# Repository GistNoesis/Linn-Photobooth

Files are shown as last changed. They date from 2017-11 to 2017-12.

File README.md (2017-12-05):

# Linn Photobooth

LINN is your personal photobooth robot artist. 

A photobooth is a setup where guests take pictures of themselves.

LINN is a 2-axis gimbal controlled by a bluetooth ps3-controller which then stylize your photos with some deep neural style transfer and offer single button instant print experience.

This project was realized in two weeks for the wedding of Thi-Kim & Pierre where it was a great success (lot of fun and interest generated, ~300 pictures taken, ~6000 art pieces created, ~100 prints but we ran out of paper).

Without them this project would never have existed. You can contribute to their wedding gift here : <a href="https://www.paypal.com/cgi-bin/webscr?cmd=_s-xclick&hosted_button_id=3XTEK2FP9ZW2Q"> Donate via Paypal </a>

You can donate to <a href="https://gistnoesis.net/">Gist Noesis</a> on our <a href="https://gistnoesis.net/"> main site </a> or for the photobooth project <a href="https://www.paypal.com/cgi-bin/webscr?cmd=_s-xclick&hosted_button_id=UNQ332GV5MSDU"> here </a>. You can also use the following affiliate links and buy our recommended products to help us improve the photobooth and develop our company. 

You can also help us grow by Starring our repository, sharing it on social media, or even better by building your own Linn.

It's free for non-commercial use. 

It exists in different variants depending on the budget you want to spend, your technical abilities, and the internet connectivity of the event location.

Here is the full setup which went live :

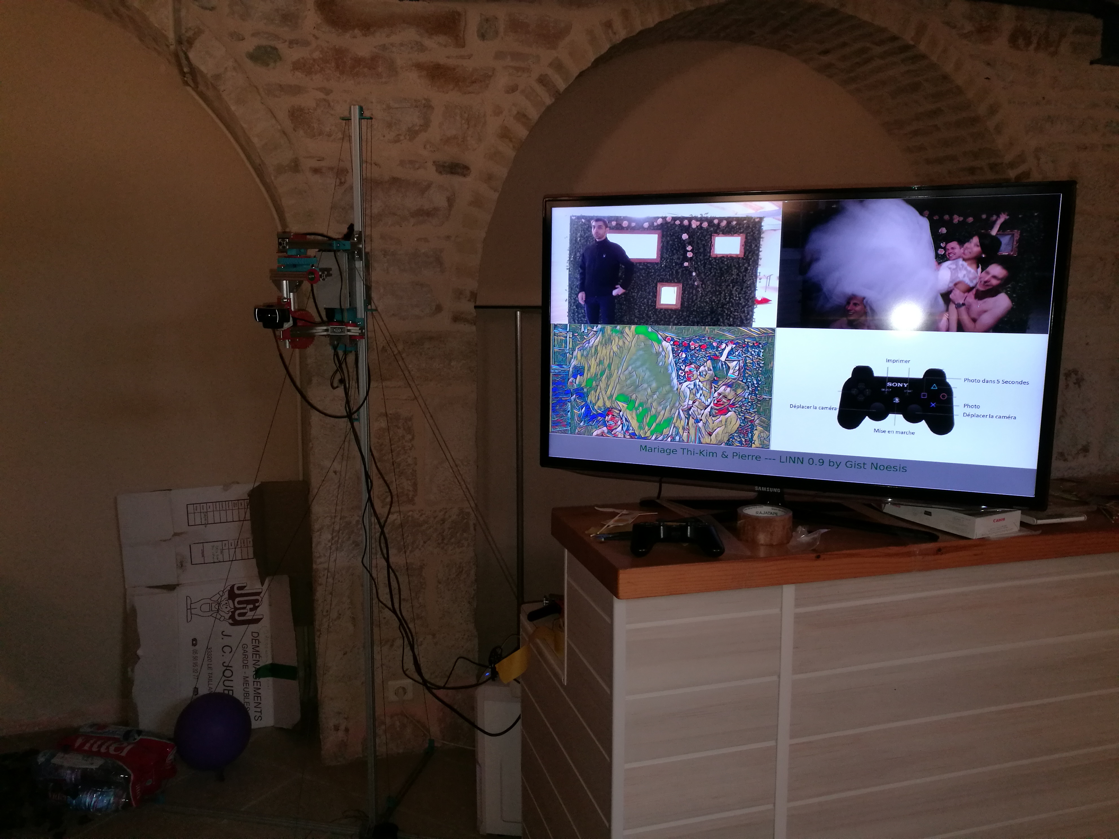
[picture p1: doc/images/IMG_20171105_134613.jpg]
Picture of the full setup


The user experience is intended streamlined : the users put themselves with accessories in the frame of the camera, they see themselves on the TV so they can see what the photo looks like,
 then press X on the controller and it takes a photo instantly displayed. Then they either press Select two times to print the original pictures and 30 secs later they have the printed photo.
Alternatively they can use L2/R2 to change the art style, wait less than 6 secs then press Start two times to print the art picture. 
They can also press "Square" to have the photo taken in 5 secs (enough to hide the ps3 controller).
They can also use L1/R1 to see previous/next pictures.
They can also use the analogic joystick to move the camera.
If you enable manual auto exposure using v4l2-ctl -d /dev/video0 -c exposure_auto=1 then the up and down arrows will adjust exposure time. (Remember you can also adjust Gain using v4l2-ctl to play on ISO sensitivity)

Prototype Demo :

Demo in video (https://www.youtube.com/watch?v=Dvh4kFYVPd0)

Update with GT2 pulley :

Update with GT2 pulley (https://www.youtube.com/watch?v=oYx7XjZQiro)

Advanced human tracking :

Advanced human tracking (https://www.youtube.com/watch?v=4UNtOUySp14)

# Hardware : 
- <a target="_blank" href="https://www.amazon.fr/Manette-PS3-Dual-Shock-noire/dp/B00167U0HY/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">PS3 controller Dual shock 3</a> (I used a controller from my ps3, cheaper clones will probably work, I charged mine and it had enough battery for the night, but you can buy a spare one)
- Bluetooth dongle (<a target="_blank" href="https://www.amazon.fr/Works-BT150-R%C3%A9seau-Adaptateurs-Bluetooth/dp/B00FG2WFE6/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">IT WORKS BT150</a> is lubuntu16.04 compatible It's overpriced but I bought this model at the FNAC to be sure to get it in time, there are probably some compatible bluetooth dongle for a lot cheaper https://doc.ubuntu-fr.org/bluetooth_materiel-soutenu )
- <a target="_blank" href="https://www.amazon.fr/Logitech-C922-Pro-Stream-Webcam/dp/B01L6L52K4/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">Logitech C922</a>
- Canon Selphy CP800
- TV Hd-ready (everything was developped for full HD so I had to adapt the ratio quickly when I discovered my grandparents tv was only Hd-ready )
- <a target="_blank" href="https://www.amazon.fr/Sedatech-PC-GTX1080Ti-CardReader-R%C3%A9solution/dp/B06XJ6431Q/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">Sedatech PC Gamer Ultimate Intel i7-7700K 4x 4.20Ghz (max 4.5Ghz), Geforce GTX1080Ti 11Go, 32Gb RAM DDR4 3000Mhz, 3To HDD, 500Go SSD</a>
- Second <a target="_blank" href="https://www.amazon.fr/MSI-GTX-1080-AERO-11G/dp/B06XT3983Y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">GTX 1080 Ti</a> 11Go Perfect for deep learning. Availability and price varies a lot. 
- 2 axis DIY Gimbal (2 nema 17 stepper (with their cable of appropriate length), <a target="_blank" href="https://www.amazon.fr/gp/product/B018CAVF4E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">RAMPS</a>, <a target="_blank" href="https://www.amazon.fr/Sumvision-Power-Supply-2xSATA-24PIN/dp/B00642F8AU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">PC Power supply</a> (You will need to hack it (by connecting green wire to black (gnd) wire so the power supply start));
<a target="_blank" href="https://www.amazon.fr/LogiLink-CP095-Câble-dalimentation-Schuko-C13/dp/B003Y5IG2W?&_encoding=UTF8&tag=gistnoesis04-21&linkCode=ur2&linkId=aca8e4693b3958e1ad744385ac6ee15e&camp=1642&creative=6746">Power supply cable</a> ; <a target="_blank" href="https://www.amazon.fr/StarTech-com-ATXP4EXT-dextension-dalimentation-processeur/dp/B000O7WFHA/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">ATX extension cable</a>(This cable got damaged during transport and one contact was loose) You can choose longer cables if you don't want to put the power supply near the RAMP board) , 2020 aluminum profiles aluminium brackets screws and nuts (sourced from http://www.systeal.com/fr/ ), ABS 3d printed parts, <a target="_blank" href="https://www.amazon.fr/gp/product/B00EPNN62M/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">608 bearings</a>  , <a target="_blank" href="https://www.amazon.fr/Spectra-Extreme-tresse-tressé-100-m-2000/dp/B01AYUUGYU?&_encoding=UTF8&tag=gistnoesis04-21&linkCode=ur2&linkId=a2e66e39fd9b59a4e716e9a769da290e&camp=1642&creative=6746">150kg dyneema rope</a>) 
- Two 1.8m USB A to B male cables (one for the RAMPS and one for the printer), long enough HDMI cable

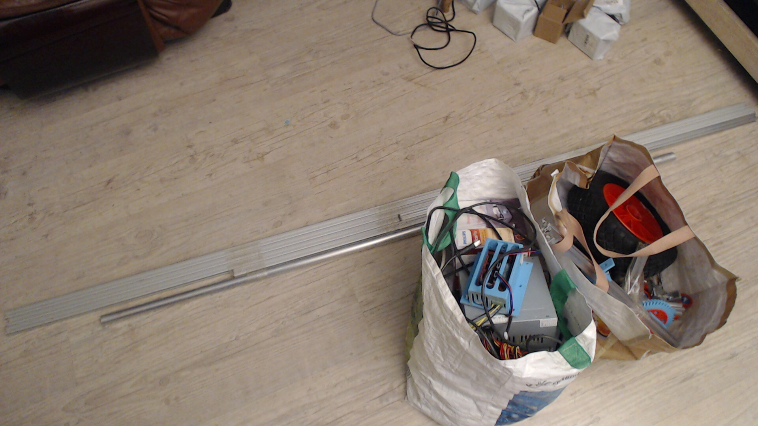
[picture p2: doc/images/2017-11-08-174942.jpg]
Packaged : Electronic in one bag, Mechanical parts and tools in the other bag
 
 Packaged : Electronic in one bag, Mechanical parts and tools in the other bag
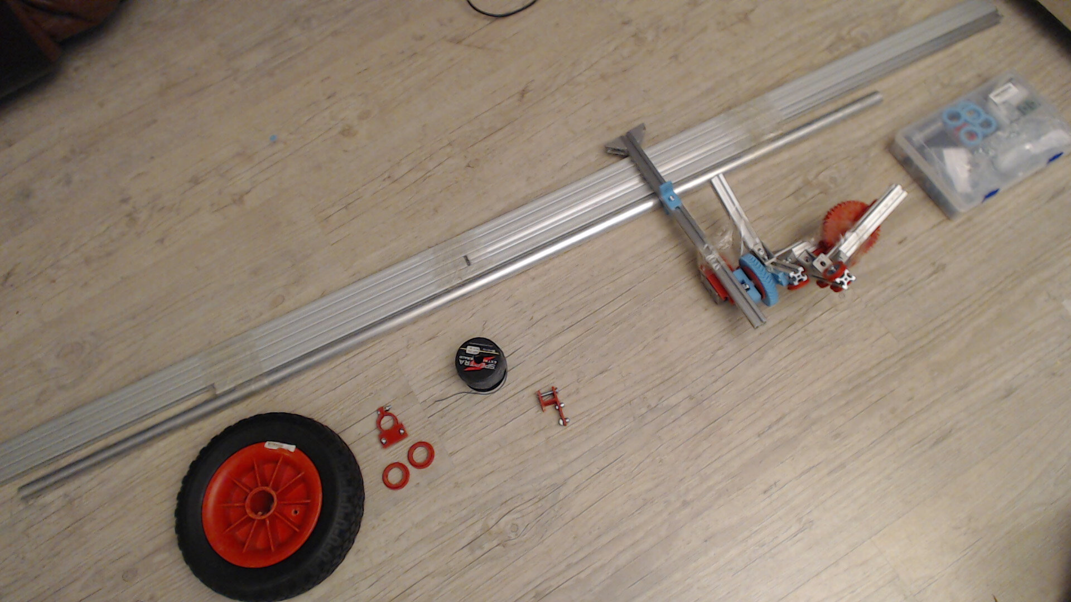
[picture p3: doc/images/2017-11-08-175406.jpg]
Unpacked : Mechanical parts two versions with and without diy gimbal
	
Unpacked : Mechanical parts two versions with and without diy gimbal
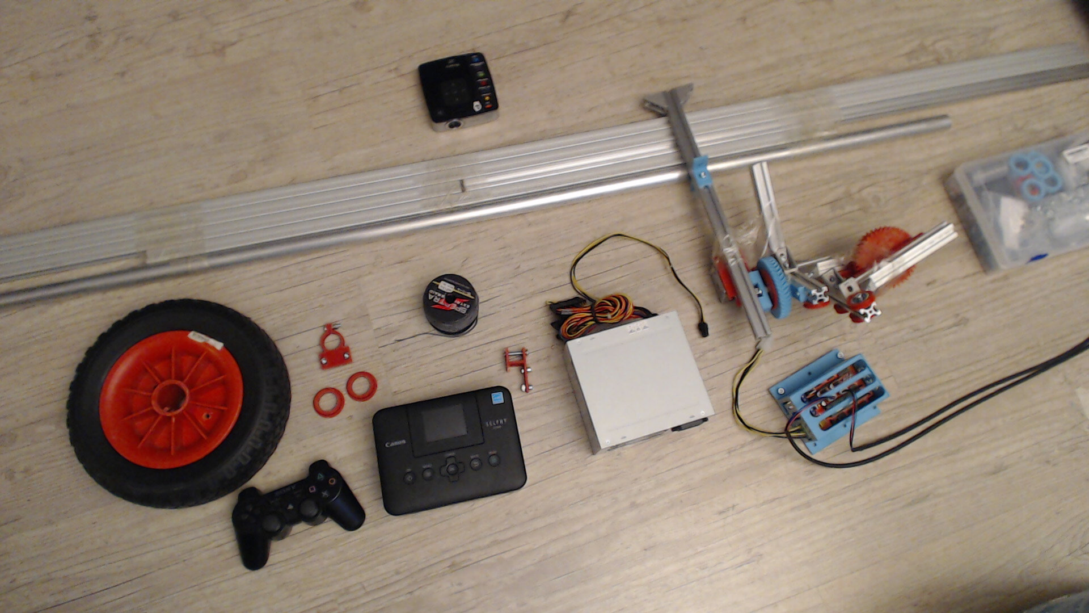
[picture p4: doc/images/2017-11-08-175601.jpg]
Unpacked : Everything except TV, cables and computer
	
Unpacked : Everything except TV, cables and computer
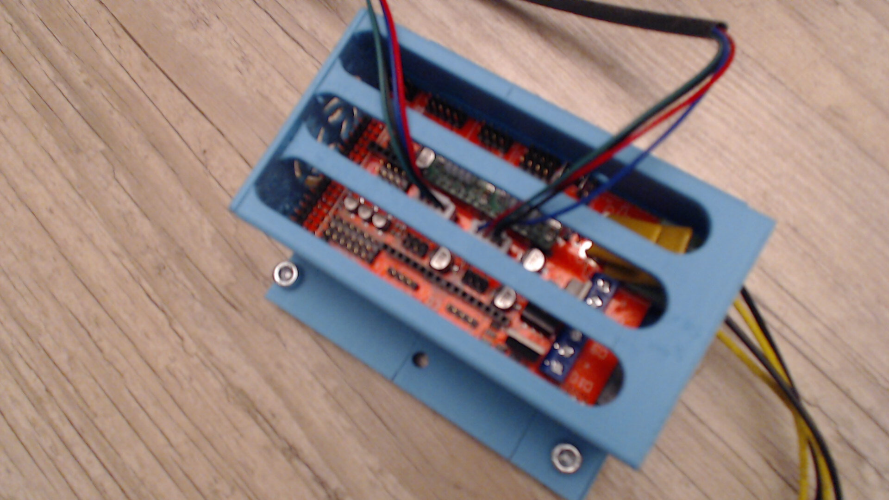
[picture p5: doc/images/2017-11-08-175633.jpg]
close up of the RAMPS board
	
close up of the RAMPS board
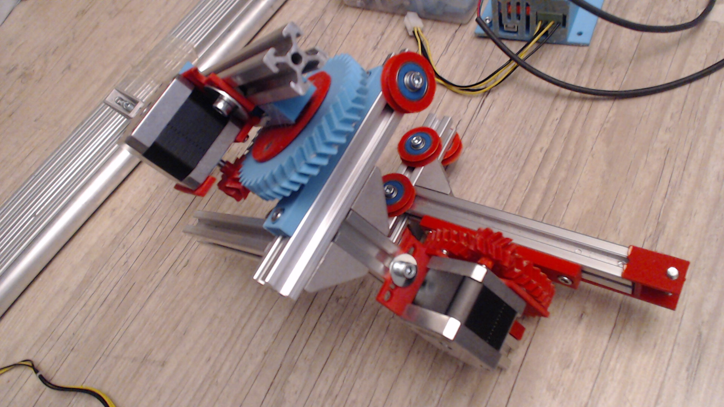
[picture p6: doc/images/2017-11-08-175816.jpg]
close up of diy gimbal
	
close up of diy gimbal
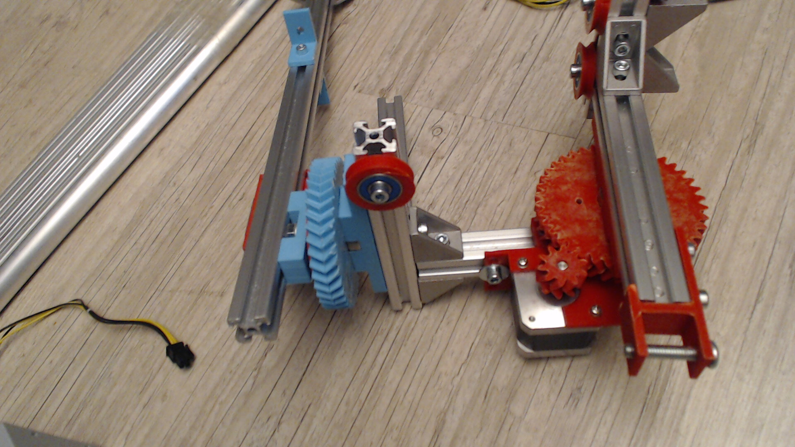
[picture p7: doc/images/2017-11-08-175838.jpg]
close up of diy gimbal other angle
	
close up of diy gimbal other angle
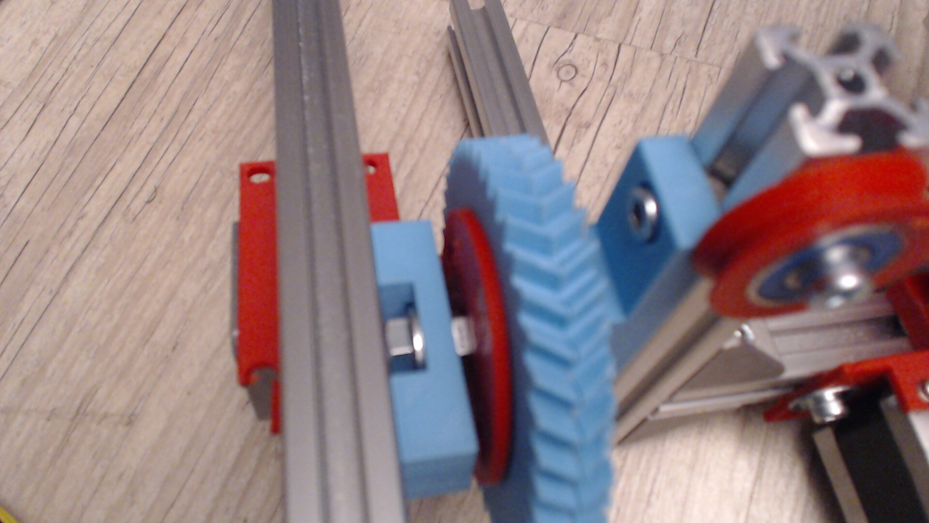
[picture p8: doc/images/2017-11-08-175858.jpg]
close up of one axis of the diy gimbal
	
close up of one axis of the diy gimbal
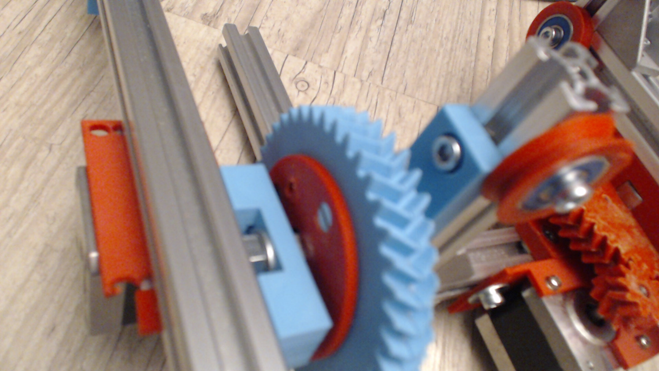
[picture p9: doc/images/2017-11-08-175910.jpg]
close up of one axis of the diy gimbal other angle
	
close up of one axis of the diy gimbal other angle
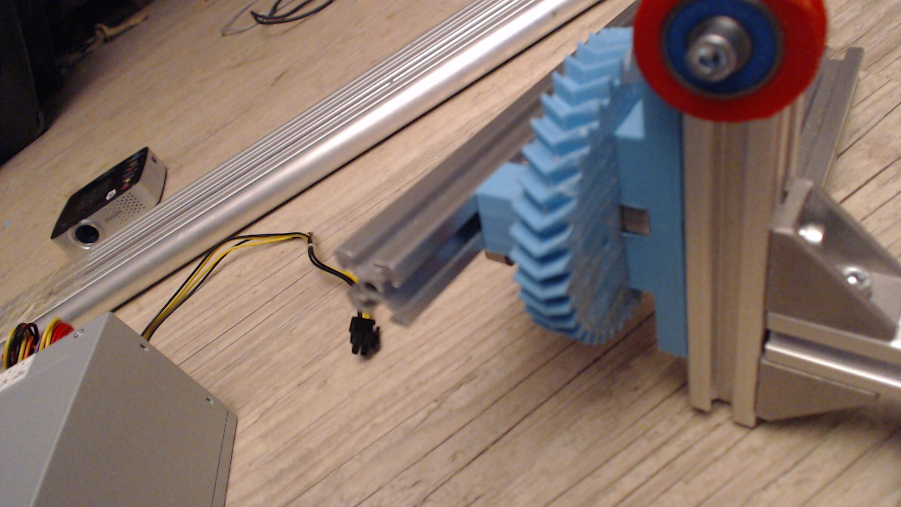
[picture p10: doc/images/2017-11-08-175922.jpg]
close up of one axis of the diy gimbal yet another angle
	
close up of one axis of the diy gimbal yet another angle
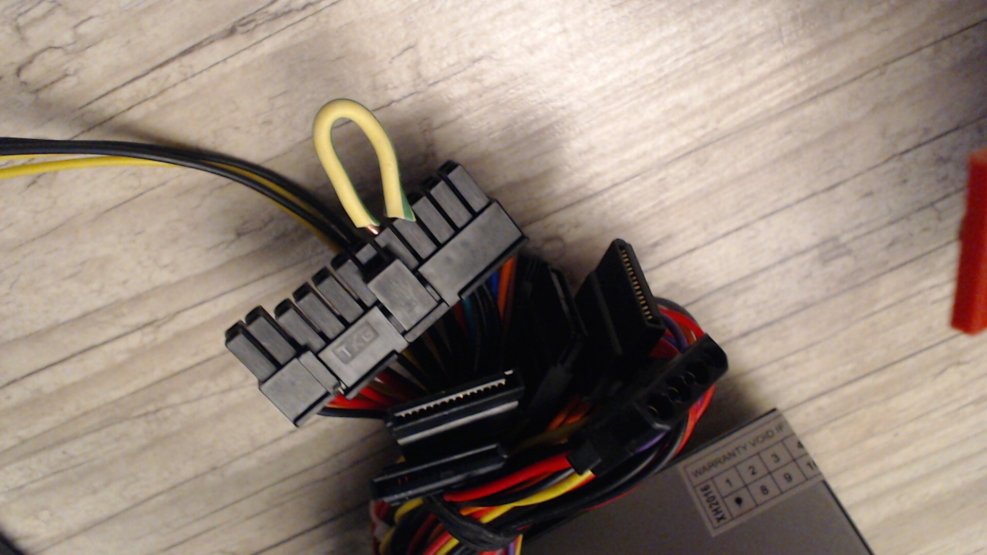
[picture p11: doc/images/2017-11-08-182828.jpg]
connecting the green wire to the black wire to enable the power supply

connecting the green wire to the black wire to enable the power supply

# Software : 
You can install it by docker (see docker folder
(I'll add a guide soon to help build the software stack or follow the dockerfile, but for the remote art I'll probably do it)

- Lubuntu 16.04 (for its ability to Undecorate windows)
- OpenCV (You need to install from source so you can properly show images : I've followed https://medium.com/@debugvn/installing-opencv-3-3-0-on-ubuntu-16-04-lts-7db376f93961 install with python3 support )
- Python3 ( I've used a virtualenv as you probably should, I've not yet listed the dependencies in requirements.txt (damn OpenCv) : numpy pyserial evdev zmq)
- Sixad (driver for bluetooth ps3 controller installed from source)
- Arduino IDE (You need to add your current user to the dialout group to resolve serial permission issues) (Load the ino project, Install AccelStepper Library using "Sketch->Include Library->Manage Library Select board Mega 2560 and serial /dev/ttyUSB0 and then upload)
- Fast-Neural-style (https://github.com/jcjohnson/fast-neural-style) (Remember to update torch : see https://github.com/jcjohnson/fast-neural-style/issues/137 ) (Called by remoteart.sh replace "beast" in script by username@yourartserverip and make sure you can ssh without password to this machine before using ssh-copy-id)

# The variants :

If you have a good internet connectivity you don't need a PC with GPUs as the scripts are customizable to dispatch jobs over ssh to process the art. 

- So you can use a cheaper PC and rent some amazon cloud for the night.
- The webcam C922 or the older more famous <a target="_blank" href="https://www.amazon.fr/Logitech-microphone-int%C3%A9gr%C3%A9-compatible-Facebook/dp/B006A2Q81M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">Logitech C920</a> are only full HD, if you have extra money you should probably invest in the 4K resolution <a target="_blank" href="https://www.amazon.fr/Logitech-Business-Brio-Conférence-Enregistrement/dp/B01N5NYRES/?&_encoding=UTF8&tag=gistnoesis04-21&linkCode=ur2&linkId=d38f295892f9729b255d6cacbbed4d48&camp=1642&creative=6746">Logitech Brio</a> on a USB3.0 port (and adapt the code a little to set the resolution to 4K). (I have not tested the linux compatibility). 
- The TV can be substituted by some video projector like <a target="_blank" href="https://www.amazon.fr/Philips-PPX3417W-Vid%C3%A9oprojecteur-DLP-Noir/dp/B01DY5QXLC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">PicoPix video projector</a> if you have a good control of the lighting conditions (people should be in the light but video projected image should be in the dark and are ready to sacrifice some display quality for ease of transportation.
- The 2-axis DIY Gimbal can be substituted either with the small tripod which come with the C922 or with an aluminium pole and some 3d printed pole adapter parts. (change UseDummySerial to True in code if you don't use RAMPS)
- The PS3 controller can be substituted by a bluetooth keyboard (currently only space to take a picture is supported).
- The printer is not necessary, as print requests are saved to a file. You probably can use <a target="_blank" href="https://www.amazon.fr/Canon-0599C002-Selphy-CP1200-Noir/dp/B01AAVMJHU/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">Selphy CP1200</a> as a replacement for the old CP800 or any other printer. Just check they are linux compatible (gutemberg). Buy compatible ink+paper combo in advance.
-Pulleys or gears : pulleys are a lot smoother are there is no more backlash but you need to buy some closed GT2 belt (6mm wide > 300mm length (not too long for the vertical axis) Remember to invert the axis between gears and pulleys if facetracker goes in the wrong direction :) 

# The attention to detail :

Although this was only a 2-week project, I took care of a lot of small details which contributed a lot to the success :
- Safe (Low 12V voltage), very stable due to large base, well balanced, quite light,  well delimited by cables and water bottle packs so that people don't trip into it or go under overhanging arm, not very strong so it can't harm fingers if people touch it, can be turned manually and stay in position even without power, TV taped to the table so it won't accidently fall.
- Cheap and reusable
- Software end stop for the camera movement, so users can't break the camera or mingle the cables, (even though without the end stop camera collisions are not to severe and are probably fine)
- Analogic speed variation for the camera movement
- Robust handling of errors (by calling subprocesses) and exceptions, so the program should not crash even when controller is disconnected or run out of battery
- Pre-print confirmation and acknowledgement of print
- Instant response via multithreaded application
- Partial documentation centered on the essential, but with some of the guests knowing the extra features to help new users.
- Capturing extra frames before (yes circular buffer trick :) ) and after pictures were taken (so we can do later some super resolution if necessary to compensate for 2MP sensor). We can have some extra footage of pre picture preparation.
- Correct prioritization depending on current selected art and picture of the art stilization tasks to mask as much as possible the computation time.
- Processing in the background when inactive all the different styles so that they are all computed.
- Delete with confirmation (not a real delete but a move to deleted picture folder so people can erase picture either for private pictures)
- Reset button of the RAMPS pressable at any time without crashing the software if necessary
- The program can be stopped by pressing "q" and when it restarts it recompute missing styles so you can add new styles and have a consistent art database
- You can use v4l2-ctl to manually adjust some additional camera settings, like auto focus, gain, auto exposure, sharpness, backlight compensation, zoom (if you opt for the Brio), 
- The positionning of the TV with respect to the camera. As people will natually look toward the TV, you should take care that the angle between TV and camera give some good photos.
- Lighting : avoid as much as possible light behind the guests, eventually use additional light panel if you have extra money.
- Portrait vs Paysage : Both modes have been implemented. We chose Paysage for the party so that more people could be on the picture. Portrait would be better for single person from shoes to hat pictures. (set "ang" to one of 0 90 180 270 in code)
Currently we can't switch easily between both modes (i.e. displaying portraits while taking Paysage) except by relaunching the program in the other mode
- The photos were saved on the HDD the art was processed on the SSD, so I've always had 2 copies of the pictures to prevent data loss (If you have internet access you can rsync your folder to a remote directory or cloud drive)
- Using the power supply fans to assure the air flow over the ramp board.
- Easily adjustable cable tension by sliding brackets and weights.
- We customized the neural styles by training our own styles. (~3 hours to train a style)

# Making it fun : 
- We had some background picture frames where people can put their heads through, it induced a lot of funny but lower quality pictures.
- LINN can dance, if you loosen the cables you can make the camera oscillate quite a lot as the aluminium structure is intended flexible. (Be careful about nuts and bolts remaining tight enough if you push it a lot vibrations may make them loose over time) 
- You can increase the speed of the movement, disable the software endstops (so you don't care about missing step at high speed)
- I didn't have time to implement some auto tracking features for the party but you have all the pieces necessary to do it from python (And I'll probably add them if I have some spare time).
- You can probably add some automatic camera movement, and suggest photos to guests.
- You can probably add some active damping. 
- You can probably add some laser pointer to the gimbal and do some baloon popping.

# What went wrong or could be improved :
- Amazon was late for paper/ink delivery, we receive the extra paper/ink only on the next day, so we only had ~ 110 photos which we run through quite fast.
- Printer worked great, guests even reloaded the paper themselves, but they didn't understood that you should change ink and paper simulaneously as implicitely suggested by the ink/paper combo packaging so you are guarantee to have a good quality print. 
- I had to change the ink (very easy on this printer), so not yet fully autonomous, We probably should display a message on screen when ink level are low.
- Cables didn't have enough tension, so there was a little too much oscillations when moving. (Remember to test in real conditions : (while drunk :) ) )
- The ATX power supply extension cable got damaged during the transport, and one contact was loose.
- I had to reset (press the arduino button) once the RAMPS board as one axis of the motor was not responding. (It was a software bug about the arduino timer looping around every 72 minutes that I've corrected since).
- The partial documentation caused some people to miss out on the changing of the styles. It was more prevalent among people of the older generations who had never used a PS3 controller and for which the L1/R1 L2/R2 buttons are not natural.
- The lighting environment could have been improved.
- The driver makes a little noise which can't be heared during a noisy event but you can improve using TMC2100 stepper driver with 32x microstepping.
- We can easily add some rotary encoder to the gear design for closed loop control/movement recording. (Use pin change interrupts to handle up to 5 encoder per RAMPS board)

# What went great :
- LINN is physically impressive because it takes quite a volume.
- The wireless movement control is quite magical even among the young generations.
- It got some people to speak together and explain some commands to each other.
- The instant printing (for all the times people had troubles with their printers the experience of pressing a button and having the print start instantly is fantastic, the Selphy CP800 doing multiple ink-pass also contribute to the fun of it.
- The neural art makes some nice unusual visual effects.
- People discovered on their own how they could get a second examplary for their printed photo
- Overall it was great fun.

# Instructions to build the 2-axis DIY gimbal (I'll make a video if the project receive enough attention) :
The 2020 aluminum profiles are 4x 15cm, 1x 10cm, 1x 40cm these dimensions can probably be adjusted or varied and if proper balance is taken care of it will be OK.

All parts must be printed 100% infill.

Both axis are identical, their parts must be assembled in a specific order : 
They consist of :

 8mm diameter 4cm long threaded bolt, 1mm metallic spacer, short support, nut
You may add an extra 1mm metallic spacer if you wish
Then attach the support to the aluminium profile.

pulleymountspacer, two-half gears on their 608 bearings, one 608 bearing ,  nut, 

Then tighten the nut now. You can also use a lock nut instead for extra safety.
Then mount the long pulleyMount on the last bearing
Use the 2x 4mm diameter 2.5cm long conical head screw with matching nut to attach the gears to the pulleyMount by placing the nuts in the hexagonal holes

Then attach the long pulleyMount to the aluminum profile.

The support and pulleyMount must be printed in the correct orientation (i.e. 2cm height) to provide good strength
The two-half gears should be marked so that they are correctly aligned (It's very error prone), and gears should be pointed in the correct direction. 
(I designed it in two half parts so that in an attempt to reduce backlash by having the top wheel a little offset)

You can then print without support the supportstepper and piniongear (remember to adjust the diameter to the diameter of your stepper motor so that the fit is tight.

# The secrets of robot arms : Proper balance
The center of mass of a rotating part should be as near as possible to the axis of rotation. You can use extra bearing with 10mm t-slot nuts and screw to balance the arm. (Remember to balance with the camera in position and orientation)
If you equilibrate properly it shouldn't rotate in either direction due to its own weight. This means that even when you have no power the arm shouldn't move.
Start by equilibring the axis which support the camera, then when it's well balance move to the next axis. You can add a lot of axis and everything will be balanced.
When the arm is well balanced you don't need a lot of force to move it and vibrations will be minimal.
Additionally in a gimbal the optical axis should be aligned with the axis of rotations or parallax effects will appear (Which can then be used to get extra 3d information).

# The support : 
This can vary quite a lot.
The wider the base the more stability. At a minimum the base should be longer than the arm so that there is no overhang. 
LINN was 2 meter height and a cross of 2 meter and 2 times 1 meter. I mounted the ramps board in its box on the pole, added the power supply on top so that air flows secured in place by cable, tape and an equerre5
Without water bottle counter weight When pushed its tendency was rather to slide away rather than tilting.
Doubling the aluminum profile can increase rigidity a lot.

# The cable system : 
It's time for you to reveal your inner spider.
I didn't have to cut my rope at all.
Use equerre5 (again printed in 2cm height direction) to thread some cables to increase the rigidity of the structure. You can slide them to increase the tension. The aluminium profile should bend.
Then when you will add some counter weight on the extremities to reduce the bending it will increase the tension even more. If you have a musical hear you can even tune them in harmony.
If these sort of designs interest you, you will probably be interested by the tensegrity concept (which we are not an instance of). 
You should construct your cable system so you can adjust the height of the robot arm quite easily and then you can easily tense the cable again by sliding some equerre5. The long support cross helped in this regard.

# Not yet included features : 
-Video : you can probably do it in a few lines using the unassigned "circle" button (recording while the button is pressed) and save frame like it's done for extra frames), remember to display message indicating that it's currently recording and to handle the case where controller is disconnected. Getting the audio and encoding and synchronisation will be more complex.
-Serving the photos and art to a webserver where you could vote for the best pictures or style
-Serving the photos live to twitter

# What's next : 
At Gist Noesis we have some robotics division, where we design and print low cost customizable robots safe for the home. 
We are aiming for safe, cheap, robust, reusable and customizable but sacrificing look, precision and repeatablity.
If LINN get enough attention and enough donations we may hire someone to improve it, provide ready to rent boxes for events, or sell kits.
LINN may also interest some video streamers especially those not yet famous one which can use it as a cheap cameraman.
LINN can be converted in a 3d scanner turn table.

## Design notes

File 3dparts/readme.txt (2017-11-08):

In this folder goes the 3d printed parts openscad files and stl.

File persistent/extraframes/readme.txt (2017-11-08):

In this folder we will store the extra frame which you can later use for super resolution or mini videos

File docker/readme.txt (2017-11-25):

Docker currently working but still a work in progress to make it more user friendly. I'll put it on dockerhub when fully functional
Currently working from a lubuntu 16.04 host, (with ps3 controller working),  though there is still some configuration
I took https://github.com/fcwu/docker-ubuntu-vnc-desktop as a starting point 

build using : 
docker build -t linn-photobooth . 

run the image using (set mypassword to the password you want to use and the persistent folder path):
If you need all functionalities (i.e. bluetooth ps3 controller) you will need to give more permissions
docker run --privileged  --cap-add=ALL --net=host --device=/dev/video0:/dev/video0 -v /lib/modules:/lib/modules -v /var/run/dbus:/var/run/dbus -v ABSOLUTE_PATH_TO_HOST_LINN-PHOTOBOOTH_PERSISTENT_FOLDER:/root/Linn-Photobooth/persistent -p5900:5900 -p6080:80 -e VNC_PASSWORD=mypassword linn-photobooth

Otherwise use :
docker run --privileged --net=host --device=/dev/video0:/dev/video0 -v ABSOLUTE_PATH_TO_HOST_LINN-PHOTOBOOTH_PERSISTENT_FOLDER:/root/Linn-Photobooth/persistent -p5900:5900 -p6080:80 -e VNC_PASSWORD=mypassword linn-photobooth

Then connect via vnc :
either vncviewer -fullscreen localhost:5900
or go to http://localhost:8080

Inside the container 

cd /root/Linn-Photobooth

<Optional : For remote art>
Configure remoteart.sh with your art server username and ip
Make sure you can ssh without password inside your artserver using ssh-copy-id
</Optional>
Then
python3 photobooth.py

Check that files are correctly saved inside both host and container

If you use the persistent folder it will use ROOT permissions so when you are finished on host 
you can get your original permissions back with sudo chown -R username persistent

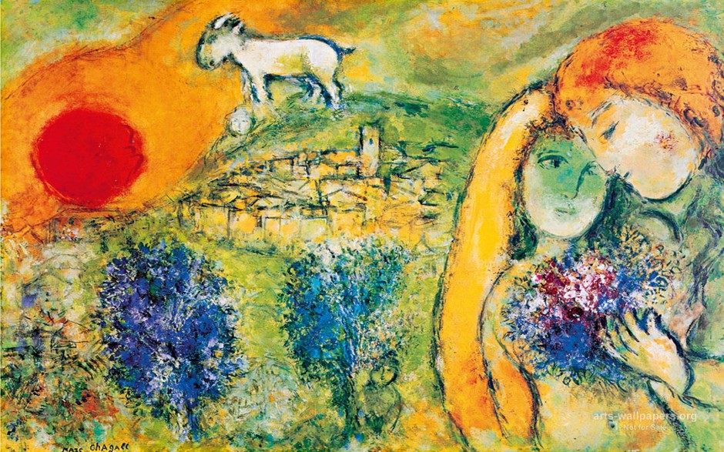
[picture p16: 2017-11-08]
styles/marc-chagall-wallpaper.jpg

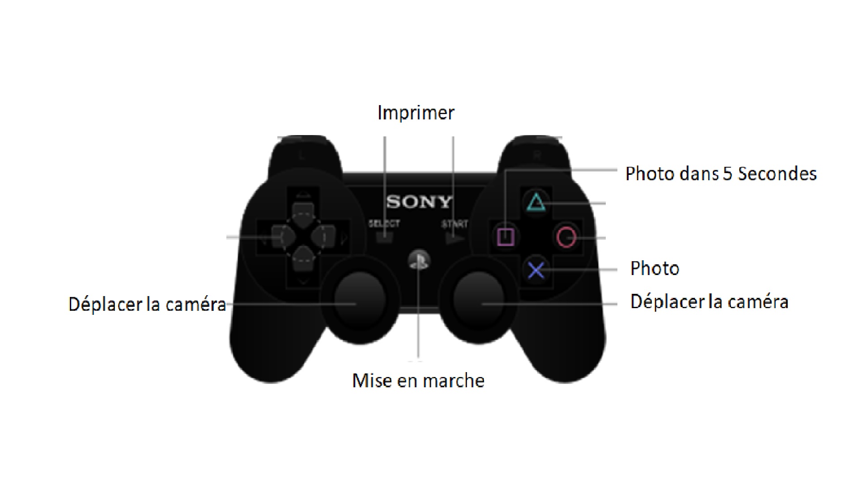
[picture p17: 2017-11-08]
ps3.jpg

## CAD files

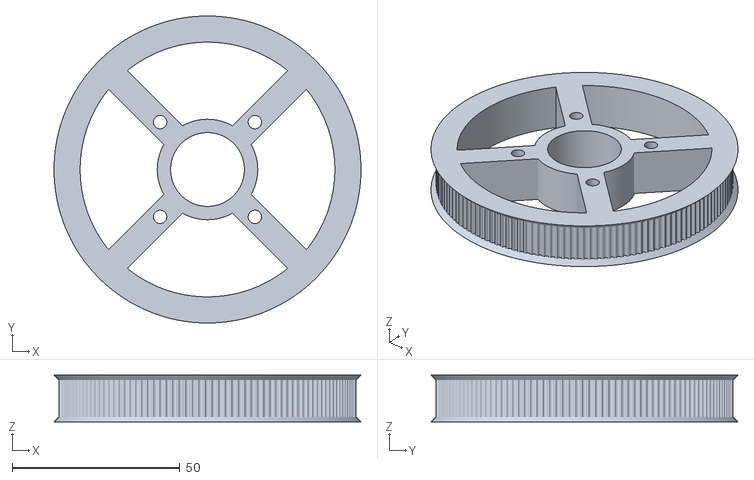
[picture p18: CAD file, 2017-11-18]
3dparts/GT2140sparsecenter.stl
91.6 x 91.6 x 14.0

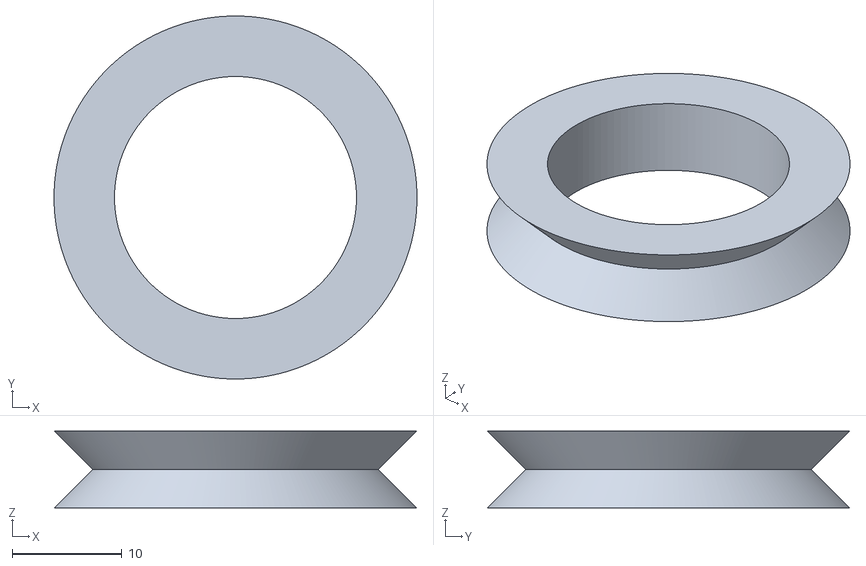
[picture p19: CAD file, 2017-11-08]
3dparts/pulleyroller.stl
33.0 x 33.0 x 7.00

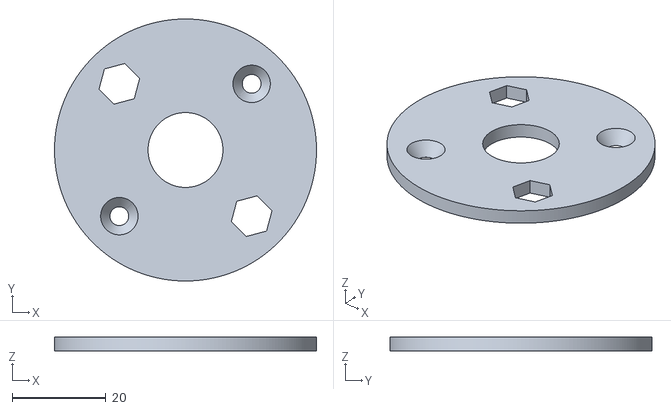
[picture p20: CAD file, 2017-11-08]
3dparts/pouliemountspacer.stl
56.0 x 56.0 x 3.00

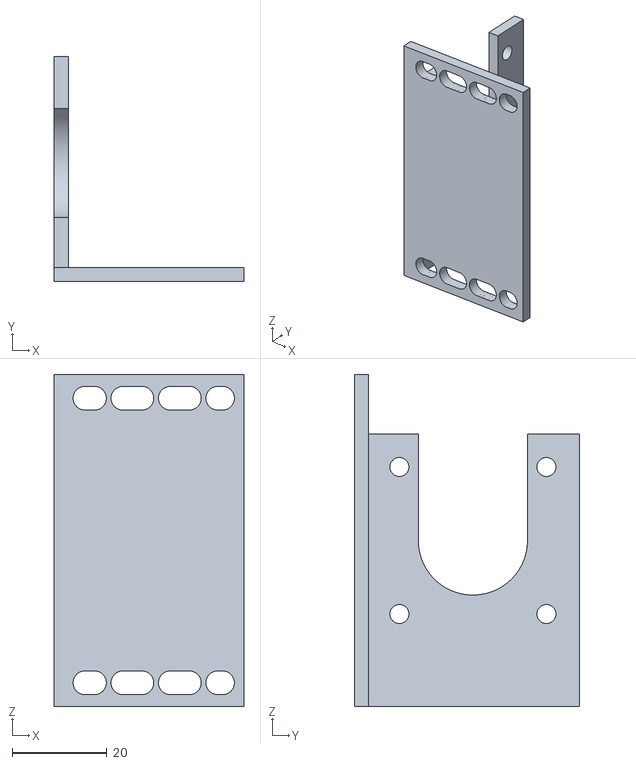
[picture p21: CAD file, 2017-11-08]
3dparts/supportstepper.stl
40.0 x 47.5 x 70.0

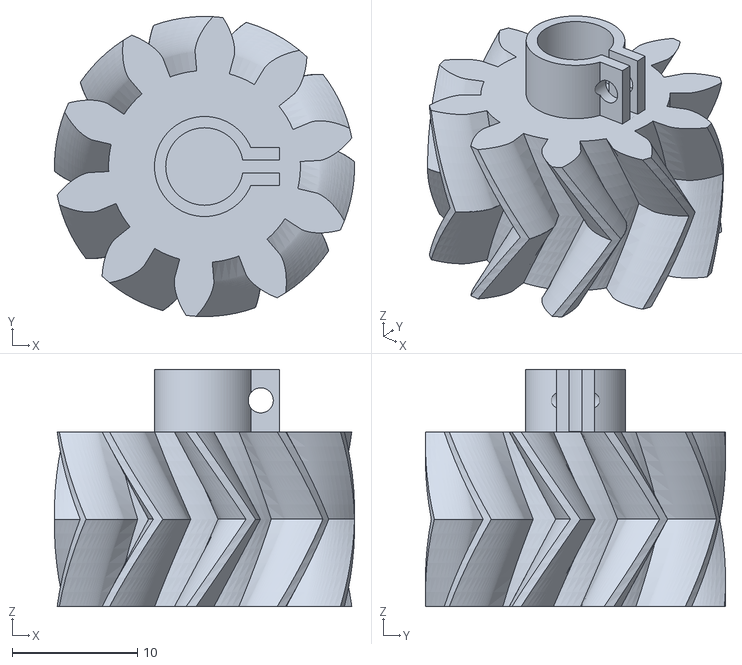
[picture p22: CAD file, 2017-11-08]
3dparts/piniongear.stl
24.0 x 24.0 x 19.0

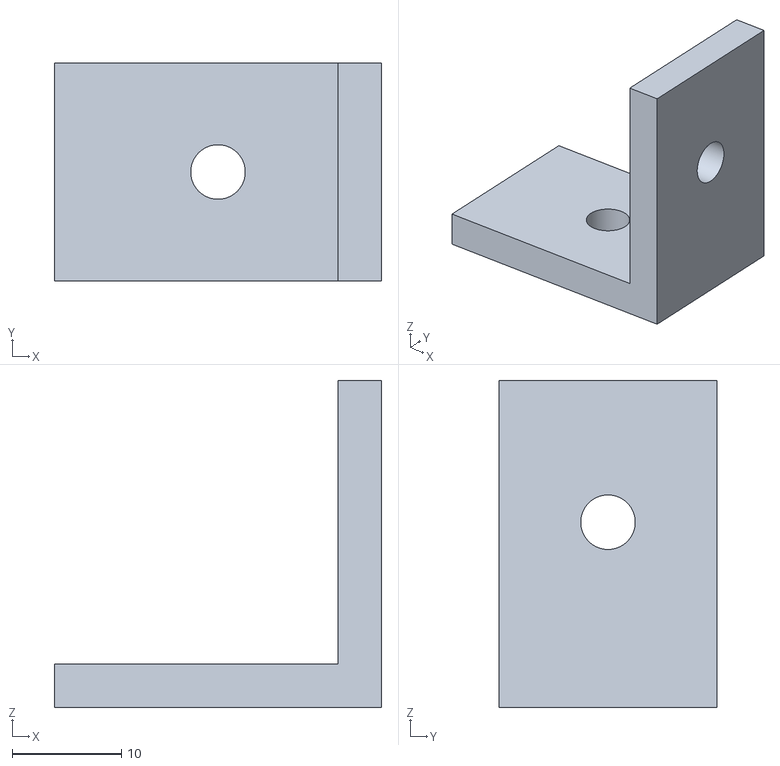
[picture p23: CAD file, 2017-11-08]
3dparts/equerre5.stl
30.0 x 20.0 x 30.0

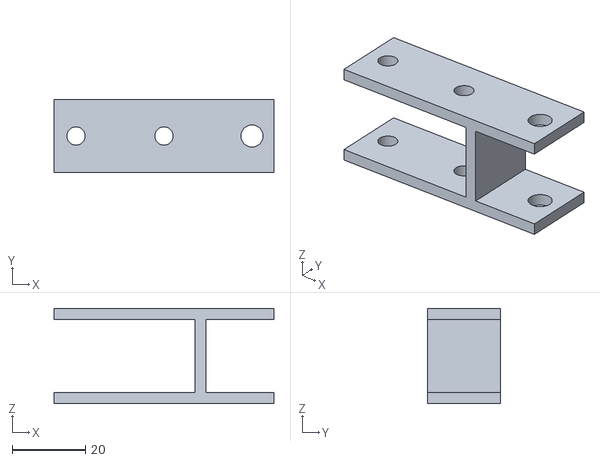
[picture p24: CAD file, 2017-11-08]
3dparts/cameramount.stl
60.0 x 20.0 x 26.0

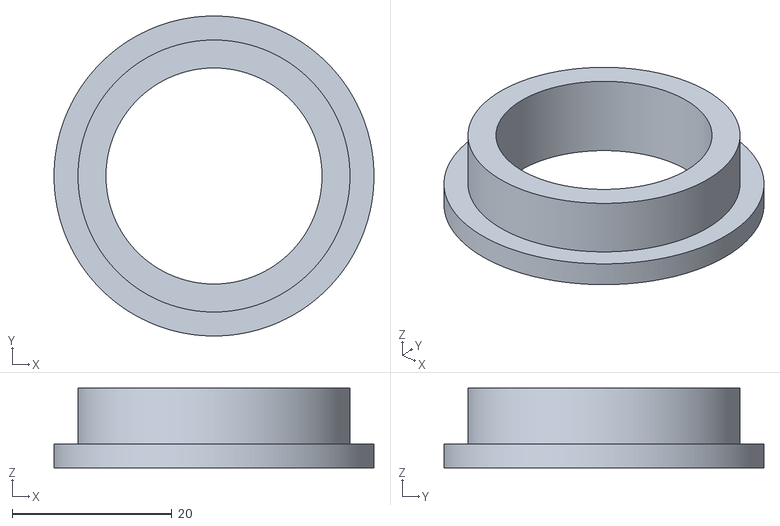
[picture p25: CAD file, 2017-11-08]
3dparts/poleadapter.stl
40.0 x 40.0 x 10.0

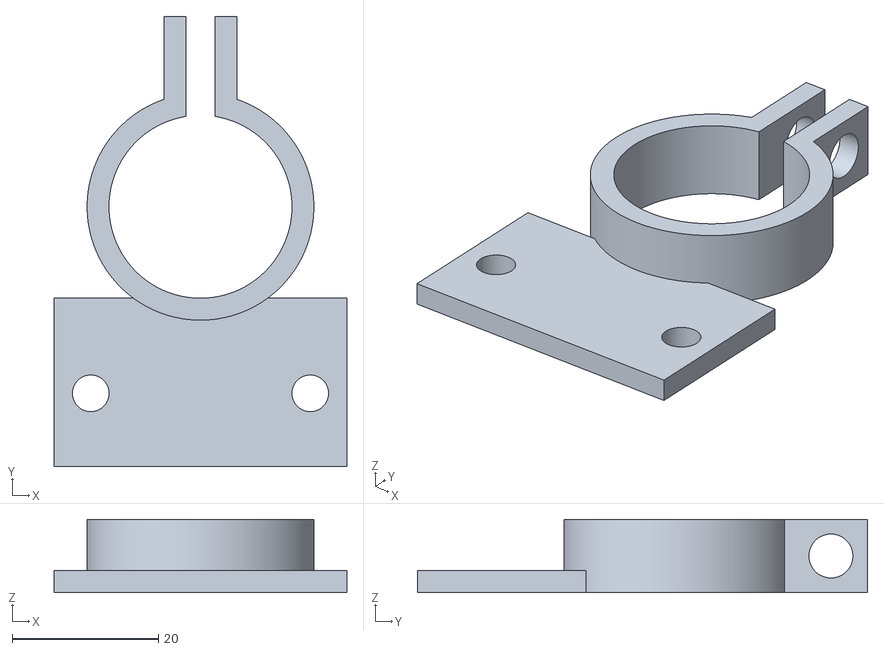
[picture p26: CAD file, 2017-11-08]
3dparts/polemount.stl
40.0 x 61.5 x 10.0

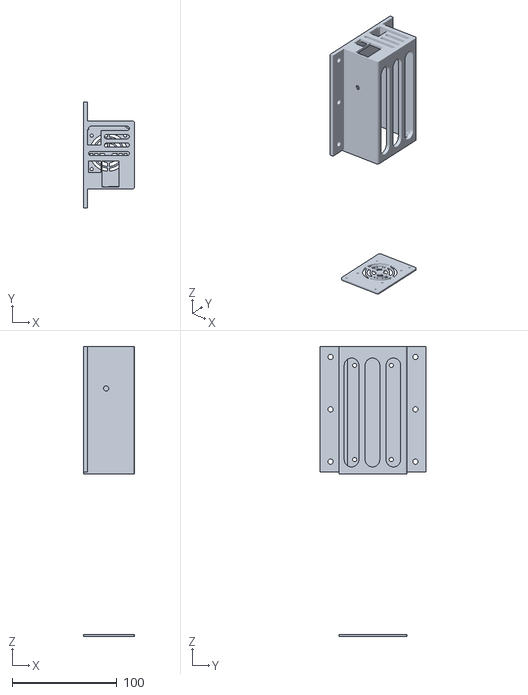
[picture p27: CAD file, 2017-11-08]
3dparts/ramps-wind-box.stl
49.0 x 101.0 x 277.0

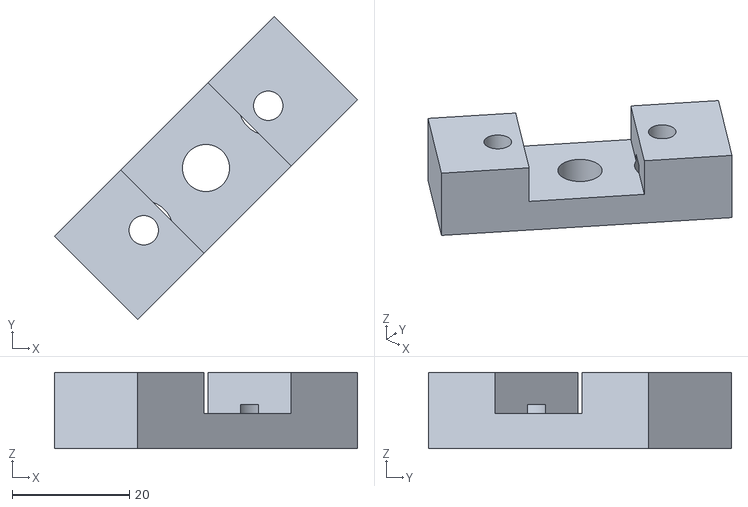
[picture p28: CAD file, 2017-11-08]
3dparts/yawsupportflat2.stl
51.6 x 51.6 x 13.0

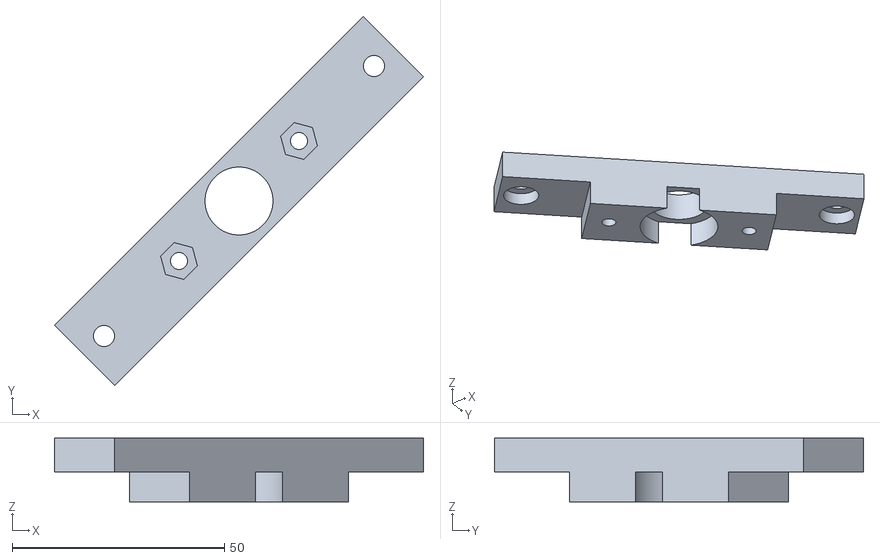
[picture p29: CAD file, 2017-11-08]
3dparts/yawpouliemountflat.stl
87.0 x 87.0 x 15.0

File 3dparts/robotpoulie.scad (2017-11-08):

include <Getriebe.scad>



module attachpulleyholes(h)
{
    union()
{
    rotate([0,0,45])
    for (deg = [0:90:(360-1)] )
    {
        rotate( [0,0,deg])
        translate([20,0,0])
        cylinder( r=2,h=2*h,center=true,$fn=200);
    }
    
}

    
    
}

radius608=11.0;

module gear(h,nbteeth,flip,angle)
{

difference()
    {
rotate([flip,0,0])
translate([0,0,-h/2])
stirnrad(2, nbteeth, h, 2*radius608, 20, angle);

union()
        {
    //    translate([20,0,0])
    // cylinder( r=5, h=20,center=true);      
attachpulleyholes(h);
        }

    }

}




module piniongear(h,nbteeth,r=3)
{
 fixh = 5;
union()
{
rotate( [0,180,0])
translate([0,0,-h/2-0.01])
stirnrad(2, nbteeth, h, 5, 20, -30);
    
translate([0,0,h/2-0.01])
stirnrad(2, nbteeth, h, 5, 20, 30);
translate([0,0,h+7/2])
difference()
{
union()
{
translate([0,0,fixh/2-0.02])
cylinder( r = 4, h=fixh, center= true);
translate( [3,0,fixh/2-0.02] )
    cube( [6,3,fixh],center=true);
}
union()
{
translate([0,0,fixh/2])
cylinder( r = r,h=fixh+ 0.01,center=true);
translate( [3,0,fixh/2] )
    cube( [6.01,1,fixh+0.01],center=true);

translate([4.5,0,fixh/2])
rotate( [90,0,0])
cylinder( r= 1.0, h = 100, center=true);
}
}
}
}



module drivepulley( rin,rout,h)
{



difference()
{
difference()
{
union()
{
difference()
{
union()
    {
        translate([0,0,h/4])
        cylinder( r1 = rout,r2=rin, h=h/2,center=true,$fn=200);
        translate([0,0,-h/4])
        cylinder( r1 = rin,r2=rout, h=h/2,center=true,$fn=200);
        
    }
cylinder( r= 16,h=10,$fn=200);
}

cylinder( r=14,h=h,center=true,$fn=200);
}
union()
{
attachpulleyholes( h );
cylinder( r=radius608,h=2*h,center=true,$fn=200);
}

union()
{
rotate([90,0,180] )
cylinder( r =1.5,h=100,center=false,$fn=200);

translate([0,14,0])
cylinder( r =3.0,h=10,center=false,$fn=200);
}

}



}
}



module attach2020holes( e = 3)
{
    translate([0,-43,0] )
    cylinder(r=2.5,h=10*e,center=true,$fn=200);

translate([0,-58,0] )
    cylinder(r=2.5,h=10*e,center=true,$fn=200);

translate([0,-73,0] )
    cylinder(r=2.5,h=10*e,center=true,$fn=200);
}

module support( e =3)
{
difference()
{
translate( [0,-35,10])
cube( [20,90,e],center=true);
union()
{
cylinder(r=4,h=10*e,center=true,$fn=200);
attach2020holes(e);

}


}
    
    
}



module spacer( h = 3, r = 4.2)
{
    difference()
    {
    cylinder( r = r +1.5,h=h,center=true,$fn=200);
    cylinder( r = r ,h=2*h,center=true,$fn=200);
    }
}




module pouliemount( e = 4, l =60 )
{
    
    union()
    {
    difference()
    {
      cylinder( r =28, h = e, center=true, $fn=200);
      union()
        {
      cylinder( r =8, h = 2*e, center=true, $fn=200);
            attachpulleyholes(e);
            rotate([0,0,45])
            union()
            {
            for (deg = [0:180:(360-1)] )
            {
                rotate( [0,0,deg])
                translate([20,0,e-4.9])
                cylinder( r1=2,r2=4.0,h=3,center=false,$fn=200);
            }
            for (deg = [90:180:(360-1)] )
            {
                rotate( [0,0,deg])
                translate([20,0,0])
                cylinder( r=4.5,h=2*e,center=true,$fn=6);
            }
            }
            
        }
    }
        difference()
    {
        translate( [0,-20 - l/2 ,0])
        cube( [20,l,e] ,center=true);
        attach2020holes(e);
    }
    
    }   
}
    
module pouliemountspacer( e = 3 )
{
    union()
    {
    difference()
    {
      cylinder( r =28, h = e, center=true, $fn=200);
      union()
        {
      cylinder( r =8, h = 2*e, center=true, $fn=200);
            attachpulleyholes(e);
            rotate([0,0,45])
            union()
            {
            for (deg = [0:180:(360-1)] )
            {
                rotate( [0,0,deg])
                translate([20,0,e-3.0 - e/2+0.01])
                cylinder( r1=2,r2=4.0,h=3,center=false,$fn=200);
            }
            for (deg = [90:180:(360-1)] )
            {
                rotate( [0,0,deg])
                translate([20,0,0])
                cylinder( r=4.5,h=2*e,center=true,$fn=6);
            }
            }
            
        }
    }
    
    
    }   
    
    
}


    


module roll( e = 4 )
{
    difference()
    {
    cube( [20+e,20,50] ,center = true);
    union()
        {
        translate( [0,0,-e] )
        cube( [15+e,30,50] ,center = true);
         cylinder( r=4, h =100*e, center = true,$fn=200);
         
         translate( [0,0,-5] )
            {
         rotate([0,90,0])
         cylinder( r=2.5, h =40,center=true,$fn=200);
         translate( [0,0,-15] )
         rotate([0,90,0])
         cylinder( r=2.5, h =40,center=true,$fn=200);
         translate( [0,0,15] )
         rotate([0,90,0])
         cylinder( r=2.5, h =40,center=true,$fn=200);
            }
        }
    }
        
}


module yawsupport( e=4 )
{
   difference()
    {
   union()
    {
    translate( [0,10,0] )
    cube( [20+2*e,40,20] ,center = true);
    translate([0,0,-17+7/2] )
    cube( [20+2*e,20,7+0.01] ,center = true);
    translate([0,0,-17-e/2] )
    cube( [20+2*e,20,e] ,center = true);
    } 
    union()
    {
    cube( [20,100,20+2*7+0.01] ,center = true);
    translate([0,0,-13.5])
    cylinder( r=4,h=100,center = true,$fn=200);
    translate([0,-5,0])
    rotate([0,90,0])
    cylinder( r=2.5,h=100,center=true,$fn=200);
    
    translate([0,10,0])
    rotate([0,90,0])
    cylinder( r=2.5,h=100,center=true,$fn=200);
    
    translate([0,25,0])
    rotate([0,90,0])
    cylinder( r=2.5,h=100,center=true,$fn=200);
    }
}
    
}




module yawpouliemount( e = 4 )
{
    difference()
    {
    union()
    {
    translate( [0,10,0] )
    cube( [20+2*e,40,20] ,center = true);
    translate([0,0,-18+8/2] )
    cube( [45+2*e,20,8+0.01] ,center = true);
    translate([0,0,-18-7/2] )
    cube( [45+2*e,20,7] ,center = true);
    }
    union()
    {
    cube( [20,100,20+0.01] ,center = true);
    translate([0,0,-21.5])
    cylinder( r=radius608,h=7+0.01,center = true,$fn=200);
    translate([0,0,-14.5])
    cylinder( r=8,h=9+0.02,center = true,$fn=200);
    
    translate([0,-5,0])
    rotate([0,90,0])
    cylinder( r=2.5,h=100,center=true,$fn=200);
    
    translate([0,10,0])
    rotate([0,90,0])
    cylinder( r=2.5,h=100,center=true,$fn=200);
    
    translate([0,25,0])
    rotate([0,90,0])
    cylinder( r=2.5,h=100,center=true,$fn=200);
        
    for (deg = [0:180:(360-1)] )
            {
                rotate( [0,0,deg])
                translate([20,0,-18])
                cylinder( r1=2,r2=2.0,h=14+0.02,center=true,$fn=200);
            }
            for (deg = [0:180:(360-1)] )
            {
                rotate( [0,0,deg])
                translate([20,0,-15])
                cylinder( r=4.5,h=14+0.02,center=true,$fn=6);
            }
        
    }
    
    
    }
    
}

module yawpouliemountflat( e = 4 )
{
    difference()
    {
    union()
    {
    translate([0,0,-18+8/2] )
    cube( [95+2*e,20,8+0.01] ,center = true);
    translate([0,0,-18-7/2] )
    cube( [45+2*e,20,7] ,center = true);
    }
    union()
    {
    translate([0,0,-21.5])
    cylinder( r=radius608,h=7+0.01,center = true,$fn=200);
    translate([0,0,-14.5])
    cylinder( r=8,h=9+0.02,center = true,$fn=200);

    translate([45,0,-14.5])
    cylinder( r=2.5, h=20,center=true,$fn=200);
    translate([45,0,-16.5])
    cylinder( r=5.0, h=4,center=true,$fn=200);
    
    translate([-45,0,-14.5])
    cylinder( r=2.5, h=20,center=true,$fn=200);
    translate([-45,0,-16.5])
    cylinder( r=5.0, h=4,center=true,$fn=200);
        
    for (deg = [0:180:(360-1)] )
            {
                rotate( [0,0,deg])
                translate([20,0,-18])
                cylinder( r1=2,r2=2.0,h=14+0.02,center=true,$fn=200);
            }
            for (deg = [0:180:(360-1)] )
            {
                rotate( [0,0,deg])
                translate([20,0,-15])
                cylinder( r=4.5,h=14+0.02,center=true,$fn=6);
            }
        
    }
    
    
    }
    
}

module yawsupportflat( e = 4 )
{
    difference()
    {
    union()
    {
    translate([0,0,-18+7/2-e/2] )
    cube( [75+2*e,20,7+0.01+e] ,center = true);
    translate([0,0,-18-e/2] )
    cube( [45+2*e,20,e] ,center = true);
    }
    union()
    {
    translate([0,0,-18+8/2] )
    cube( [33+2*e,20+0.01,8+0.03] ,center = true);
        
    translate([0,0,-14.5])
    cylinder( r=4,h=29+0.02,center = true,$fn=200);

    translate([35,0,-14.5])
    cylinder( r=2.5, h=20,center=true,$fn=200);
    translate([35,0,-17.5-e/2])
    cylinder( r=5.0, h=4+e,center=true,$fn=200);
    
    translate([-35,0,-14.5])
    cylinder( r=2.5, h=20,center=true,$fn=200);
    translate([-35,0,-17.5-e/2])
    cylinder( r=5.0, h=4+e,center=true,$fn=200);
        
    
    }
    
    
    }
    
}
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

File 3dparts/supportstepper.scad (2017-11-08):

module nemaPlate(wallThickness=3)
{
    wallThickness = 3;
    motorWidth = 45;
    bolt = 4;
    bolt2 = 5;
    difference()
    {
        union()
        {
            cube( [wallThickness, motorWidth, motorWidth], center=true);
           
        }
   rotate( [0,90,0]) 
        {
           translate([0, 0, -2])
				{
					translate([15.5, 15.5, 0])
						cylinder(r=bolt/2, h=wallThickness+5,$fn=200);
					translate([-15.5, 15.5, 0])
						cylinder(r=bolt/2, h=wallThickness+5,$fn=200);
					translate([15.5, -15.5, 0])
						cylinder(r=bolt/2, h=wallThickness+5,$fn=200);
					translate([-15.5, -15.5, 0])
						cylinder(r=bolt/2, h=wallThickness+5,$fn=200);

					cylinder(r=11.5, h=wallThickness+5,$fn=200);
                    rotate([0,0,90])
                    {
					translate([-11.5, 0, 0])
						cube([23, motorWidth, wallThickness+5]);
                    }
				}
        }
		
        
    }
}

e=3;

nemaPlate(e);
l=70;
sp = 30;

rotate([-90,0,0])
difference()
{
union()
    {
translate([20-e/2,0,-22-e/2])
cube([40,l,3],center=true);
translate([0,30-e,-0]) 
cube([3,16,45+0.01],center=true);
    }
union()
    {
    for (x = [5:1.0:34] )
    {
        if( round(x / 5) %2 !=0 )
        {
        translate([x,sp,0])
        cylinder(r=2.5,h=100,center=true,$fn=100);
        translate([x,-sp,0])
        cylinder(r=2.5,h=100,center=true,$fn=100);
        }
        
    }
        
}   
}

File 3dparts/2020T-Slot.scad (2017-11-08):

/** 
 * @file
 * Generic library for fractional T-Slot extrusions.
 *
 * Creative Commons Share Alike 3.0
 * Copyright (c) 2014 Manuel García
 *
 * Original library (David Lee Miller)
 * https://www.thingiverse.com/thing:136430
 * 
 * Modified to be used in customizer
 */ 

//CUSTOMIZER VARIABLES

ProfileCore = 4.3 * 1;     // Profile core Ø (Default M5).
minkR_TS = 0.04 * 20;  // Minkowski radius for the T-Slot.
minkR_IC = 0.075 * 20; // Minkowski radius for the inner cutout.
minkR_PF = 0.05 * 20;  // Minkowski radius for the profile corners.


height_in_mm = 20;

//2020Profile(height_in_mm);

//CUSTOMIZER VARIABLES END

module 2020Profile(height, core = ProfileCore) {
  linear_extrude(height = height, center = true)
  union() {
    difference() {
      minkowski() {
        translate([0, 0, 0]) circle(r = minkR_PF, center = true, $fn = 32);
        square([1 * 20 - 2 * minkR_PF, 1 * 20 - 2 * minkR_PF], center = true);
      }
      translate([0, 0, 0]) circle(r = core / 2, $fn = 24);
      translate([-0.5 * 20 + 0.087 * 20, 0, 0]) tSlot();
      rotate([0, 0, 180]) translate([-0.5 * 20 + 0.087 * 20, 0, 0]) tSlot();
      translate([0, -0.5 * 20 + 0.087 * 20, 0]) rotate([0, 0, 90]) tSlot();
      translate([0, 0.5 * 20 - 0.087 * 20, 0]) rotate([0, 0, -90]) tSlot();
    }
  }
}

module fillet(rad) {
  translate([-rad, -rad, 0])
  difference() {
    translate([0, 0, 0]) square([rad + 0.01, rad + 0.01]);
    circle(r = rad, center = true, $fn = 32);
  }
}

module insideCutout() {
  minkowski() {
    translate([0, 0, 0]) circle(r = minkR_IC, center = true, $fn = 32);
    hull() {
      square([0.2 * 20 - minkR_IC, 0.645 * 20 - 2 * minkR_IC], center = true);
      square([0.8 * 20 - 2 * minkR_IC, 0.001 * 20], center = true);
    }
  }
}

module doubleCutout() {
  union() {
    minkowski() {
      translate([0, 0, 0]) circle(r = minkR_IC, center = true, $fn = 32);
      union() {
        rotate([0, 0, 0]) hull() {
          translate([-0.5 * 20, 0, 0]) hull() {
            square([0.2 * 20 - minkR_IC, 0.645 * 20 - 2 * minkR_IC], center = true);
            square([0.8 * 20 - 2 * minkR_IC, 0.001 * 20], center = true);
          }
          translate([0.5 * 20, 0, 0]) hull() {
            square([0.2 * 20 - minkR_IC, 0.645 * 20 - 2 * minkR_IC], center = true);
            square([0.8 * 20 - 2 * minkR_IC, 0.001 * 20], center = true);
          }
        }
        rotate([0, 0, 90]) hull() {
          translate([-0.5 * 20, 0, 0]) hull() {
            square([0.2 * 20 - minkR_IC, 0.645 * 20 - 2 * minkR_IC], center = true);
            square([0.8 * 20 - 2 * minkR_IC, 0.001 * 20], center = true);
          }
          translate([0.5 * 20, 0, 0]) hull() {
            square([0.2 * 20 - minkR_IC, 0.645 * 20 - 2 * minkR_IC], center = true);
            square([0.8 * 20 - 2 * minkR_IC, 0.001 * 20], center = true);
          }
        }
      }
    }
    rotate([0, 0, 0]) translate([-0.645 * 20 / 2, -0.645 * 20 / 2, 0]) fillet(minkR_IC);
    rotate([0, 0, 180]) translate([-0.645 * 20 / 2, -0.645 * 20 / 2, 0]) fillet(minkR_IC);
    rotate([0, 0, 90]) translate([-0.645 * 20 / 2, -0.645 * 20 / 2, 0]) fillet(minkR_IC);
    rotate([0, 0, -90]) translate([-0.645 * 20 / 2, -0.645 * 20 / 2, 0]) fillet(minkR_IC);
  }
}

module tSlot() {
  union() {
    translate([minkR_TS, 0, 0])
    minkowski() {
      translate([0, 0, 0]) circle(r = minkR_TS, center = true, $fn = 32);
      hull() {
        square([0.001 * 20, 0.585 * 20 - 2 * minkR_TS], center = true);
        translate([(0.233 * 20 - 2 * minkR_TS) / 2, 0, 0]) square([0.233 * 20 - 2 * minkR_TS, 0.2 * 20], center = true);
      }
    }
    translate([-0.255 * 20 / 2 + 0.01, 0, 0]) square(0.255 * 20, center = true);
    translate([-0.35 * 20 / 2 - 0.087 * 20 + 0.01, 0, 0]) square(0.35 * 20, center = true);
    translate([0, -0.255 * 20 / 2, 0]) fillet(minkR_TS / 2);
    translate([-0.087 * 20, -0.255 * 20 / 2, 0]) rotate([0, 0, 90]) fillet(minkR_TS / 2);
    scale([1, -1, 1]) translate([0, -0.255 * 20 / 2, 0]) fillet(minkR_TS / 2);
    scale([1, -1, 1]) translate([-0.087 * 20, -0.255 * 20 / 2, 0]) rotate([0, 0, 90]) fillet(minkR_TS / 2);
  }
}

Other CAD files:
3dparts/cameramount.scad
3dparts/GT2140sparse.scad
3dparts/Getriebe.scad
3dparts/ramps-wind-box.scad
3dparts/rampsbox.scad

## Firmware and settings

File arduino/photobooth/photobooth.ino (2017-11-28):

typedef struct  {
  int ENABLE_PIN;
  long lowerBound;
  long upperBound;
  bool speedMode;
} StepperExtras;


// Pins for the RAMPS board
const int X_STEP_PIN         = 54;
const int X_DIR_PIN          = 55;
const int X_ENABLE_PIN       = 38;  // Active LOW

const int Y_STEP_PIN         = 60;
const int Y_DIR_PIN          = 61;
const int Y_ENABLE_PIN       = 56;  // Active LOW

const int Z_STEP_PIN         = 46;
const int Z_DIR_PIN          = 48;
const int Z_ENABLE_PIN       = 62;  // Active LOW

#include <AccelStepper.h>
#include <stdio.h> // for function sprintf

AccelStepper XAxis2( AccelStepper::MotorInterfaceType::DRIVER,X_STEP_PIN,X_DIR_PIN );
AccelStepper YAxis2( AccelStepper::MotorInterfaceType::DRIVER,Y_STEP_PIN,Y_DIR_PIN );

StepperExtras XAxis = {X_ENABLE_PIN,-2700,2700,true};
StepperExtras YAxis = {Y_ENABLE_PIN,-3700,3700,true};

void setup() {
   Serial.begin(115200);   
  // put your setup code here, to run once:
  pinMode(LED_BUILTIN, OUTPUT);
  pinMode(X_STEP_PIN, OUTPUT);
  pinMode(X_DIR_PIN, OUTPUT);
  pinMode(X_ENABLE_PIN, OUTPUT);

  pinMode(Y_STEP_PIN, OUTPUT);
  pinMode(Y_DIR_PIN, OUTPUT);
  pinMode(Y_ENABLE_PIN, OUTPUT);

  
  digitalWrite( X_STEP_PIN, 0 );
  digitalWrite( Y_STEP_PIN, 0 );

  digitalWrite( X_ENABLE_PIN, 0 );
  digitalWrite( Y_ENABLE_PIN, 0 );

  digitalWrite( X_DIR_PIN, 1);
  digitalWrite( Y_DIR_PIN, 0 );

  XAxis2.setAcceleration(10000.0);
  YAxis2.setAcceleration(10000.0);
  
  XAxis2.setMaxSpeed(20000);
  YAxis2.setMaxSpeed(20000);
}


typedef struct {
  byte pin : 6;
  byte mode : 1;
  byte state : 1;
} DigitalPin;

void set(DigitalPin& pin,boolean mode=INPUT,boolean state=false)
{
 pin.mode = mode;
 pin.state = state;
 pinMode( pin.pin, pin.mode);
 digitalWrite( pin.pin, pin.state);
}









void pollWithEndStop( AccelStepper& stepper,StepperExtras& extra)
{
  if( stepper.currentPosition() >= extra.upperBound && stepper.speed() > 0.0 )
  {
    stepper.setSpeed( 0.0 );
    extra.speedMode=true;
  }
  if( stepper.currentPosition() <= extra.lowerBound && stepper.speed() < 0.0 )
  {
    stepper.setSpeed( 0.0 );
    extra.speedMode=true;
  }

  if( extra.speedMode )
  {
    stepper.runSpeed();
  }
  else
  {
    stepper.run();
  }
  
}




char intBuffer[15];
String intData = "";
int delimiter = (int) '\n';

unsigned char curl = 0;
bool stringready = false;
void ProcessSerial()
{
  if( Serial.available() )
  {
    int ch = Serial.read();
    if( ch == -1 )
    {
      //Handle error
    }
    else if( ch == delimiter )
    {
      stringready = true;
    }
    else
    {
      intBuffer[curl] = (char)ch;
      curl = curl+1;
      if( curl > 13 )
        curl = 0;
    }
  }

  if( stringready )
  {
    intBuffer[curl]=0;
    if( curl > 2 )
    { 
      StepperExtras *axis = NULL;
      AccelStepper * stepper = NULL;
      if( intBuffer[0] == 'x' )
      {
        axis=&XAxis;
        stepper= &XAxis2;
      }
      else if( intBuffer[0] == 'y' )
      {
        axis=&YAxis;
        stepper=&YAxis2;
      }
      if( axis !=NULL)
      {
        
        if( intBuffer[1] =='s')
        {
          float f = atof(&(intBuffer[2]) );
          stepper->setSpeed((float)f);
          axis->speedMode=true;
          Serial.print( "{\"");
          Serial.print( intBuffer[0] );
          Serial.print( intBuffer[1] );
          Serial.print( "\":");
          Serial.print(f);
          Serial.println( "}");
        }
        else if( intBuffer[1] =='a')
        {
          int i = atoi(&(intBuffer[2]) );
          stepper->moveTo(i);
          axis->speedMode=false;
          Serial.print( "{\"");
          Serial.print( intBuffer[0] );
          Serial.print( intBuffer[1] );
          Serial.print( "\":");
          Serial.print(i);
          Serial.println( "}");
        }
        else if( intBuffer[1] =='r')
        {
          int i = atoi(&(intBuffer[2]) );
          stepper->move(i);
          axis->speedMode=false;
          Serial.print( "{\"");
          Serial.print( intBuffer[0] );
          Serial.print( intBuffer[1] );
          Serial.print( "\":");
          Serial.print(i);
          Serial.println( "}");
        }
        else if( intBuffer[1] =='l')
        {
          int i = atoi(&(intBuffer[2]) );
          axis->lowerBound = i;
          Serial.print( "{\"");
          Serial.print( intBuffer[0] );
          Serial.print( intBuffer[1] );
          Serial.print( "\":");
          Serial.print(i);
          Serial.println( "}");
        }
        else if( intBuffer[1] =='u')
        {
          int i = atoi(&(intBuffer[2]) );
          axis->upperBound = i;
          Serial.print( "{\"");
          Serial.print( intBuffer[0] );
          Serial.print( intBuffer[1] );
          Serial.print( "\":");
          Serial.print(i);
          Serial.println( "}");
        }
        else if( intBuffer[1] =='h')
        {
           stepper->setCurrentPosition(0);
        }
        
      }
    }
    curl=0;
    stringready=false;
  }

  
}

int loco = 0;

void PrintSerial()
{
  Serial.print("{\"pos\":[");
  Serial.print( XAxis2.currentPosition() );
  Serial.print(",");
  Serial.print( YAxis2.currentPosition() );
  Serial.println("]}");
}

void loop() { 
  ProcessSerial();
  loco++;
  if( loco == 100)
  {
    PrintSerial();
    loco = 0;
  }

  
  
  pollWithEndStop(XAxis2, XAxis );
  pollWithEndStop(YAxis2, YAxis );
  

}

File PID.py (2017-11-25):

from collections import deque


class PIDController:
    def __init__(self,t0, Kp,Ki,Kd):
        self.Kp = Kp
        self.Ki = Ki
        self.Kd = Kd
        self.output = 0
        self.I = 0
        self.t =t0
        self.recentPoints = deque()




    def AppendPoint(self, currentTime, err):
        self.recentPoints.append( (currentTime,err))
        #remove oldPoints
        while( currentTime  - self.recentPoints[0][0] > 0.5 and len(self.recentPoints)>1 ):
            self.recentPoints.popleft()

        dt = currentTime - self.t
        if len(self.recentPoints) == 1:
            D = 0
        else:
            w = 1.0
            D = (1-w)*(err -  self.recentPoints[0][1] )/ ( currentTime - self.recentPoints[0][0]) + w*(err-self.recentPoints[-2][1]) / ( currentTime - self.recentPoints[-2][0])

        if( dt < 1.0):
            self.I += dt* err
        else:
            self.I = 0

        self.output = self.Kp*err + self.Ki* self.I + self.Kd*D
        self.t = currentTime

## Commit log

2017-11-12 Bug fix freeze one axis
    [photobooth.ino]
2017-11-18 Adding GT2 pulley relevant information
2017-11-18 Now Using AccelStepper arduino library
